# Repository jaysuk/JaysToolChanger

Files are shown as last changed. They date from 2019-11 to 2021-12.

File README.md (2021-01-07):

# JaysToolChanger
Tool Changing 3D printer with a larger print volume and minimal machined parts.

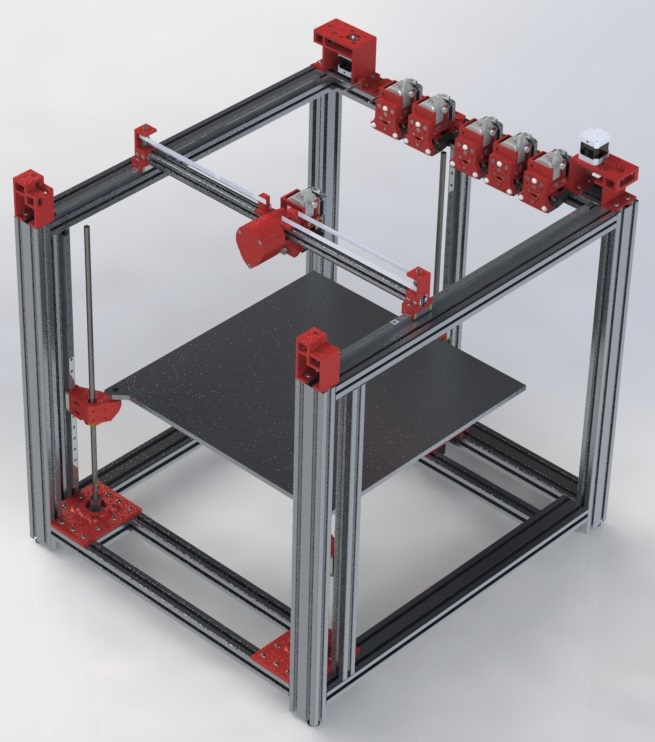
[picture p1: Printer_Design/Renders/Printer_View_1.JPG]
Printer


The design is pretty much completed and I am currently ordering and printing components.
I plan to have it built within the next couple of months or so.

# Design Goals
* Use the duet 3 board plus appropriate expansion boards
* Have direct drive tools
* Use a motor on the carriage for the tool changer (although this may be upgraded down the line to cable driven)
* Have 3 point levelling
* Have a minimal number of machined components (at the moment this stands at the bed and the locking pin).
* Design everything in Solidworks
* Stay E3D Tool compatible (my tools use 10mm balls but this wouldn't affect the tool changer)

# The todo list
These aren't in any particular order
* Design an exnclosure
* Add a method of wiping each tool
* Swap to the E3D Hermes when available
* Release duet config files
* Sort out electronics layout
* Update the bed model to include embedded magnets for swappable print surfaces
* Determine location of end stops for X, Y and Z
	
# Supplied Formats
The design will be supplied in the following file formats
* Solidworks - All files in native 2019 format. This is what I use to model everything
* Step - All files will be available as step. The assembly step files are segregated.
* STL - All printables
* 3MF - All printables
* PDF - Drawings for all machined parts

I welcome any feedback on this printer and will be working more on the design over the coming weeks.

# About Me
I'm a mechaical engineer by trade and have been dabbling in 3D printing for the last 9 years.
I have owned a number of printers, mainly cartesian or delta types. This is my first coreXY.
I plan on posting on [My Blog](https://www.jayuk.org/) with my build progression.
There is a [Discord Server](https://discord.gg/txqEmK). Come and join me for a chat!

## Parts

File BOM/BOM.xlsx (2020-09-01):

ITEM NO. | PART NUMBER | DESCRIPTION | QTY. | Purchased or Printed | Link
1 | 30x60 - 700 Front Upright | Series 6 30x60 extrusion 700mm long | 2 | Purchased
2 | 30x60 - 700 Bottom Side | Series 6 30x60 extrusion 700mm long | 2 | Purchased
3 | 30x60 - 700 Top Side | Series 6 30x60 extrusion 700mm long | 2 | Purchased
4 | 30x60 - 700 Back Upright | Series 6 30x60 extrusion 700mm long | 2 | Purchased
5 | 30x30 - 610 Z Upright | Series 6 30x30 extrusion 610mm long | 3 | Purchased
6 | 30x60 - 660 Centre | Series 6 30x60 extrusion 660mm long | 2 | Purchased
7 | 30x30 - 600 Centre Front Bottom | Series 6 30x30 extrusion 600mm long | 2 | Purchased
8 | Z Motor Mount Left |  | 1 | Printed
9 | M5x6x7 - Heat Set Insert |  | 20 | Purchased
14 | BS EN ISO 4762 M5 x 20 - 20N |  | 12 | Purchased
15 | Coupling 6.35x10 |  | 3 | Purchased
16 | 2020 Nut - M6 |  | 27 | Purchased
17 | BS EN ISO 7380 - M6 x 10 - 10N |  | 27 | Purchased
18 | Z Motor Mount Right |  | 1 | Printed
19 | Bed |  | 1 | Machined
23 | Button M3x8 |  | 20 | Purchased
24 | Rail 550mm | MGN12H Linear Rail 550mm Long with Block | 3 | Purchased
25 | 2020 Nut - M3 |  | 118 | Purchased
26 | BS EN ISO 4762 M3 x 10 - 10N |  | 118 | Purchased
27 | Z Block Left |  | 1 | Printed
28 | M3x10x5 - Heat Set Insert |  | 3 | Purchased
29 | M3x6x5 - Heat Set Insert |  | 32 | Purchased
30 | TR10 Nut |  | 3 | Purchased
31 | Ball Stud - Haydn |  | 3 | Purchased
32 | BS EN ISO 7380 - M3 x 6 - 6N |  | 14 | Purchased
33 | 30x30 - 540 Centre | Series 6 30x30 extrusion 600mm long | 1 | Purchased
34 | TR10 Thread | TR10 Threaded Rod 600mm Long | 3 | Purchased
35 | Z Motor Mount Back |  | 1 | Printed
36 | Z Block Right |  | 1 | Printed
37 | Z Block Back |  | 1 | Printed
38 | Rail 650mm | MGN12H Linear Rail 650mm Long with Block | 2 | Purchased
39 | 20x20 - 660 X Carriage | Series 5 20x20 extrusion 660mm long | 1 | Purchased
40 | Y Carriage Base |  | 2 | Printed
41 | M4x6x6 - Heat Set Insert |  | 8 | Purchased
42 | BS EN ISO 10642 - M3 x 10 - 10N |  | 4 | Purchased
43 | Y Carriage Top |  | 2 | Printed
44 | 5x7x0.3 shim |  | 22 | Purchased | https://www.aliexpress.com/item/32924107429.html?spm=a2g0s.9042311.0.0.5b684c4dTJyEaW
45 | Toothed Idler | 20t toothed idler with teeth for 10mm 2GT belt | 8 | Purchased | https://www.aliexpress.com/item/33023133633.html?spm=a2g0s.9042311.0.0.3df64c4d0Ccrgg
 | Toothed Idler | 20t toothed idler without teeth for 10mm 2GT belt | 4 | Purchased | https://www.aliexpress.com/item/33023133633.html?spm=a2g0s.9042311.0.0.3df64c4d0Ccrgg
 | 2GT Belt |  | 8m | Purchased | https://www.aliexpress.com/item/32952396111.html?spm=a2g0s.9042311.0.0.3df64c4d0Ccrgg
49 | Right Motor Mount |  | 1 | Printed
54 | Pulley | 20t Timing Belt pulley for 10mm belt | 2 | Purchased | https://www.aliexpress.com/item/33023279793.html?spm=a2g0s.9042311.0.0.3df64c4d0Ccrgg
55 | M5x10x7 - Heat Set Insert |  | 2 | Purchased
56 | BS EN ISO 7380 - M5 x 25 - 25N |  | 8 | Purchased
57 | BS 4168-3 - M5 x 10-N |  | 2 | Purchased
58 | 2020 Nut - M5 |  | 8 | Purchased
59 | BS EN ISO 7380 - M5 x 12 - 12N |  | 8 | Purchased
60 | Front Right Idler Mount |  | 1 | Printed
61 | Left Motor Mount |  | 1 | Printed
62 | Front Left Idler Mount |  | 1 | Printed
64 | MGN9-H | MGN9H Linear Rail 600mm Long | 1 | Purchased
65 | X Carriage Base |  | 1 | Printed
66 | M3x4x5 - Heat Set Insert |  | 28 | Purchased
67 | M4x10x6 - Heat Set Insert |  | 5 | Purchased
68 | 30x30 - 85 Z Motor Support | Series 6 30x30 extrusion 85mm long | 2 | Purchased
69 | 14HR08-0654S - Nema 14 Motor |  | 1 | Purchased
70 | 14t gear mod1 |  | 1 | Purchased | https://www.ebay.co.uk/itm/14T-Mod1-M1-Steel-Pinion-Gear-5mm-bore-14-tooth-hardened-rc-crawler-car/182340380462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
71 | 30t gear MOD1 |  | 1 | Purchased | https://www.ebay.co.uk/itm/30T-M1-MOD1-Steel-Pinion-Gear-hardened-5mm-bore-30-tooth-rc-car/122207015211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
72 | Locking Pin |  | 1 | Machined
73 | 91585A371 | M3 12mm dowel pin | 1 | Purchased
74 | BS 4168-2 - M3 x 2-N |  | 1 | Purchased
75 | W 605-2Z_PART1 | 6052Z bearing | 2 | Purchased | https://www.ebay.co.uk/itm/605ZZ-605-2Z-Metal-Shielded-Deep-Groove-Ball-Bearing-5x14x5mm/123276545874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
79 | Tool Changer Box Back |  | 1 | Printed
80 | Tool Changer Box Cover |  | 1 | Printed
81 | Z Switch | DB1C-A1AA | 2 | Purchased | https://smile.amazon.co.uk/dp/B00FV1TBBM/ref=pe_3187911_189395841_TE_3p_dp_1
82 | BS EN ISO 7045 - M3 x 4 - Z - 4N |  | 1 | Purchased
83 | M2x6x3.5 - Heat Set Insert |  | 2 | Purchased
84 | BS EN ISO 7380 - M4 x 12 - 12N |  | 4 | Purchased
85 | BS EN ISO 7045 - M2 x 10 - Z - 10N |  | 4 | Purchased
87 | Coupling Plate | Coupling Plate | 1 | Printed
88 | 91585A457 | M4 Dowel Pin, 20mm long | 6 | Purchased
89 | M2x8x3.5 - heat Set Insert |  | 2 | Purchased
90 | BS EN ISO 10642 - M4 x 16 - 16N |  | 3 | Purchased
91 | Main Plate |  | 6 | Printed
92 | Locking Plate |  | 6 | Printed
93 | BS EN ISO 10642 - M3 x 8 - 8N |  | 22 | Purchased
94 | m4_10mm_threaded_ ball |  | 18 | Purchased | https://www.aliexpress.com/item/32761330456.html?spm=a2g0s.9042311.0.0.5b684c4dTJyEaW
95 | BS EN ISO 10642 - M4 x 8 - 8N |  | 36 | Purchased
96 | BMG Mount |  | 6 | Printed
97 | bondtech_bmg_simplif ied |  | 6 | Purchased | https://www.aliexpress.com/item/4000072198732.html?spm=a2g0s.9042311.0.0.3df64c4d0Ccrgg
98 | E3D Hotend V6 |  | 6 | Purchased | https://e3d-online.com/v6-all-metal-hotend
105 | 17HS10-0704S - Nema 17 Motor |  | 6 | Purchased | https://e3d-online.com/slimline-motor
106 | M4x4x6 - Heat Set Insert |  | 60 | Purchased
107 | Arm Holder |  | 12 | Printed
108 | BS EN ISO 4762 M4 x 6 - 6N |  | 24 | Purchased
109 | 4010 Blower |  | 12 | Purchased
110 | Fan Mount 1 |  | 6 | Printed
111 | M2x4x3.5 - Heat Set Insert |  | 24 | Purchased
112 | Fan Mount 2 |  | 6 | Printed
113 | BS EN ISO 7045 - M2 x 5 - Z - 5N |  | 30 | Purchased
114 | Tool Holder Base |  | 6 | Printed
115 | BS EN ISO 8734 - 5 x 50 - A - St |  | 12 | Purchased | https://www.ebay.co.uk/itm/50x-Parallel-pin-dowel-pin-DIN-7-Stainless-steel-A1-A2-5X50MM/392257309488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
116 | 2020 Nut - M4 |  | 18 | Purchased
117 | BS EN ISO 7380 - M4 x 10 - 10N |  | 26 | Purchased
118 | BS 4168-4 - M4 x 5-N |  | 18 | Purchased
119 | BS EN ISO 4762 M3 x 16 - 16N |  | 12 | Purchased
120 | BS EN ISO 7380 - M6 x 12 - 12N |  | 8 | Purchased
121 | BS EN ISO 7380 - M4 x 8 - 8N |  | 4 | Purchased
122 | 2020 Nut Series 5 - M5 |  | 2 | Purchased
123 | BS EN ISO 4762 M5 x 45 - 22N |  | 2 | Purchased
124 | 2020 Nut Series 5 - M4 |  | 8 | Purchased
125 | 2020 Nut Series 5 - M3 |  | 30 | Purchased
126 | BS EN ISO 4762 M3 x 8 - 8N |  | 30 | Purchased
127 | Foot | M6 mounting foot | 4 | Purchased | https://www.ebay.co.uk/itm/Adjustable-tilt-Levelling-feet-foot-M6x25mm-kitchen-desk-table-sink-prep-bench/283463635084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
 | 24v Power Supply |  | 1 | Purchased | https://www.aliexpress.com/item/32981871190.html?spm=a2g0s.9042311.0.0.5b684c4dTJyEaW
 | Nema 23 |  | 3 | Purchased | https://www.omc-stepperonline.com/nema-23-stepper-motor/nema-23-bipolar-0-9deg-1-26nm-178-4oz-in-2-8a-2-5v-57x57x56mm-4-wires.html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
 | Nema 17 Motor |  | 2 | Purchased | https://www.omc-stepperonline.com/nema-17-bipolar-0-9deg-46ncm-65-1oz-in-2a-2-8v-42x42x48mm-4-wires-full-d-cut-shaft.html

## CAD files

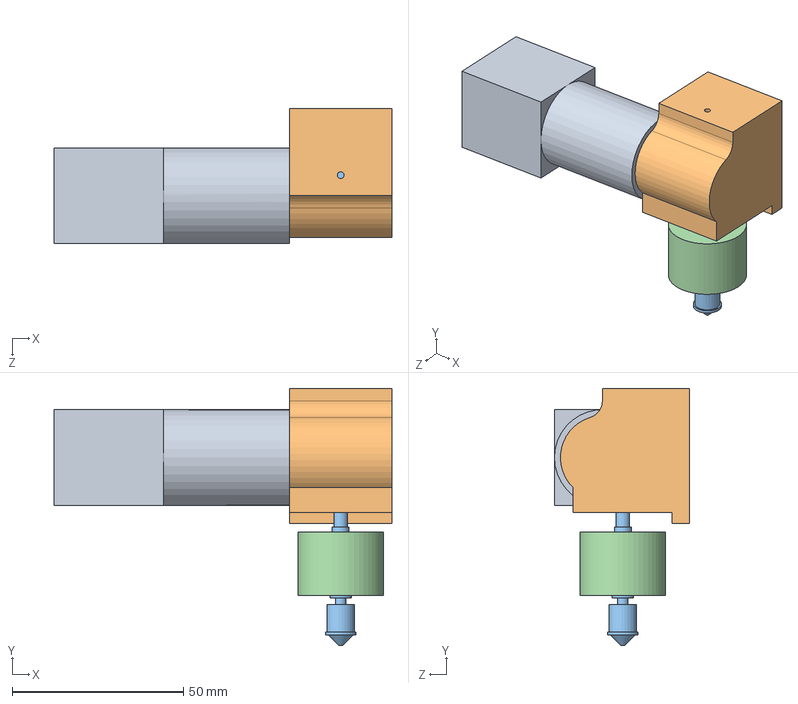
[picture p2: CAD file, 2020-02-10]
Printer_Design/Drawings/Get3D Extruder.SLDASM
98.8 x 75.2 x 39.5 mm
Motor
Extruder part 1
nozzle
Heat Sink

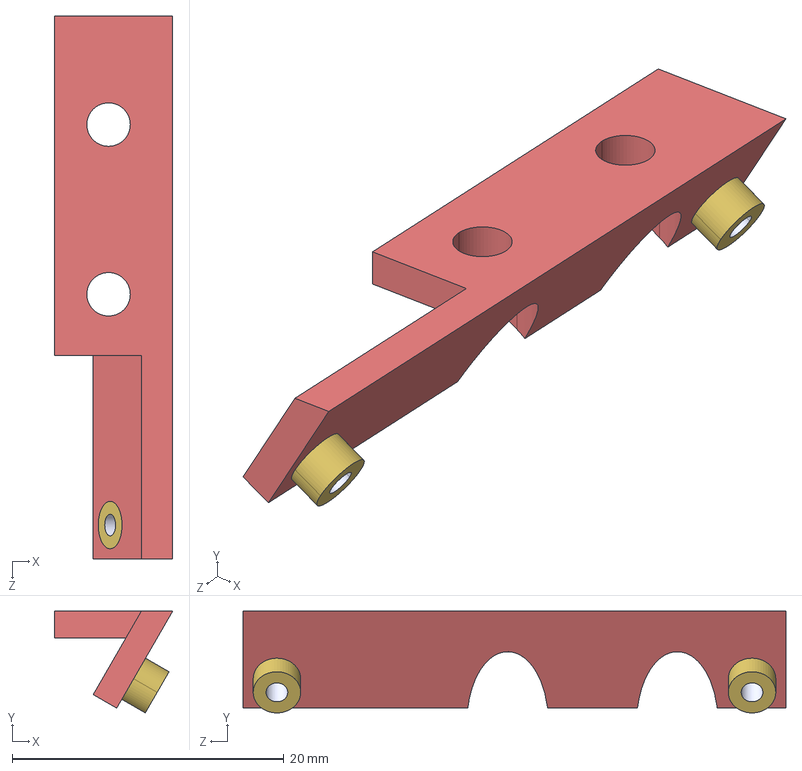
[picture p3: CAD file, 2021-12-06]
Printer_Design/STEP/Assemblies/Fan Mount 1 Assembled.step
8.73 x 7.50 x 40.0 mm
Fan Mount 1
M2x4x3.5 - Heat Set Insert x 2

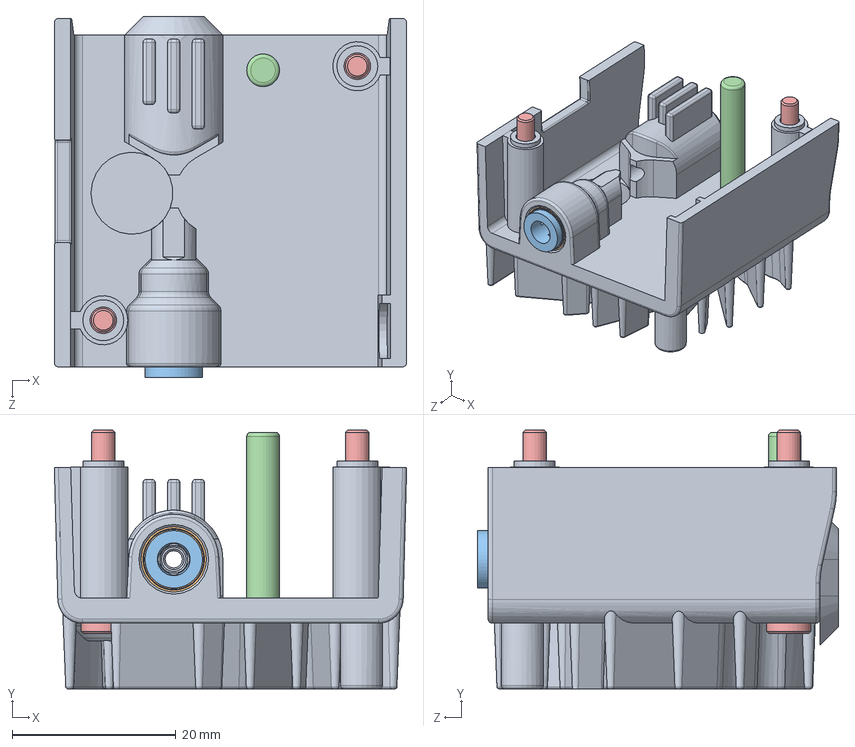
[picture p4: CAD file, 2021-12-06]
Printer_Design/Solidworks/Heatsink Assembly.sldasm
43.0 x 31.6 x 44.0 mm
Heatsink
PFTE Coupler Insert
PTFE Coupler Retainer
Lever Axis
M3x22 Hex Screw x 2

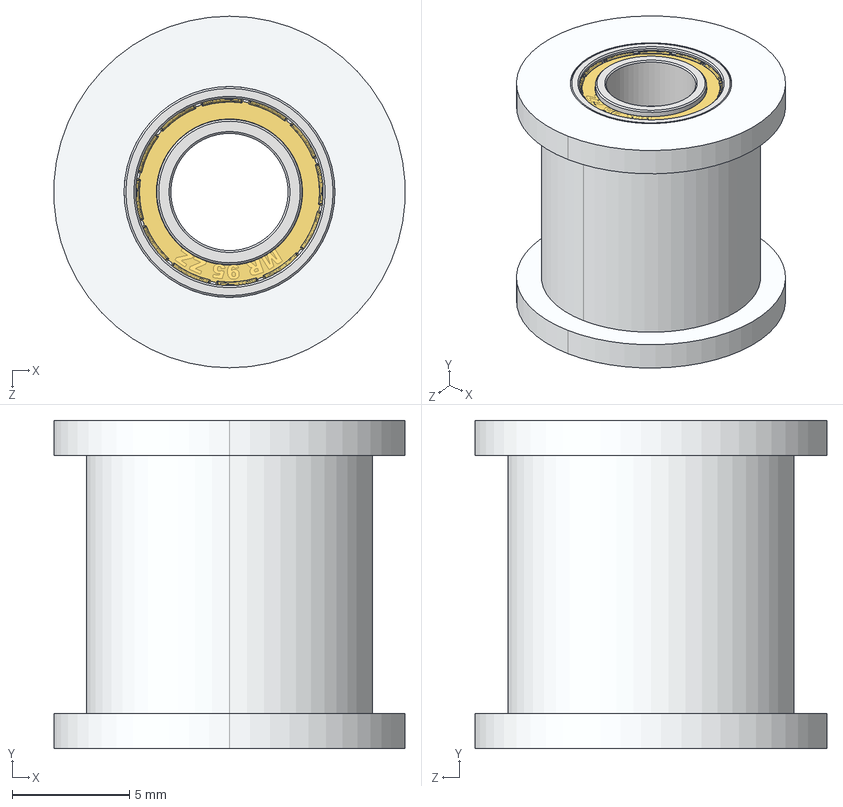
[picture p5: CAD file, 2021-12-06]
Printer_Design/STEP/Assemblies/Toothed Idler Assembled.step
15.0 x 14.0 x 15.0 mm
Toothed Idler
mr95zz-cen x 4
mr95zz-ext x 2
mr95zz-int x 2

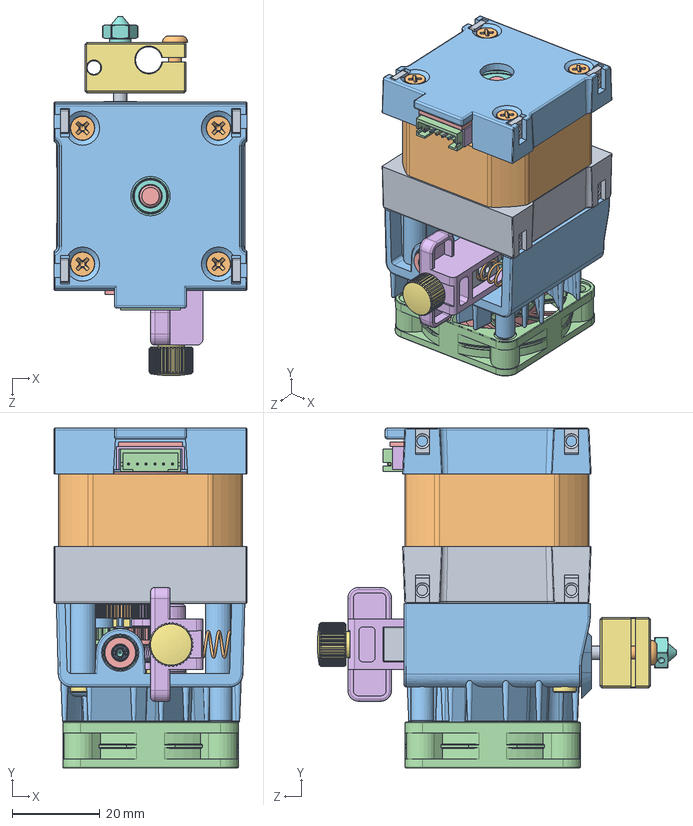
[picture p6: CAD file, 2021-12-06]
Printer_Design/Solidworks/E3D Hemera - Purchased.SLDASM
44.0 x 77.6 x 82.0 mm
Frontplate
Stator
Baseplate
ConnectrorBody (2)
PCB (3)
Insulation (2)
Axis&Rotor
Drive Gear S
Ballbearing
BallBearing2
M3 Square Nut x 9
M3x_-Screw x 4
Heatsink
PFTE Coupler Insert
PTFE Coupler Retainer
Lever Axis
M3x22 Hex Screw x 2
3.5x23.5mm Shaft (1)
10mm Bearing x 2
Drive Gear L
2.3mm Gear Spacer
Dual Transmission Gear
Filament Drive Gear Fixed
Lever Arm
Tensioner Spanner
Tensioner Push-Block
Tensioner Spring-Block
Spring
Gear Axis
4x6x8 Igus Bushing
Dual Transmission Gear (1)
Filament Drive Gear
Heater Block
Nozzle
Heat Break
M3 Button Head Screw
M3 Grub Screw
Fan Housing
Fan Propeller
M3x13 Self-Cutting Screw x 2

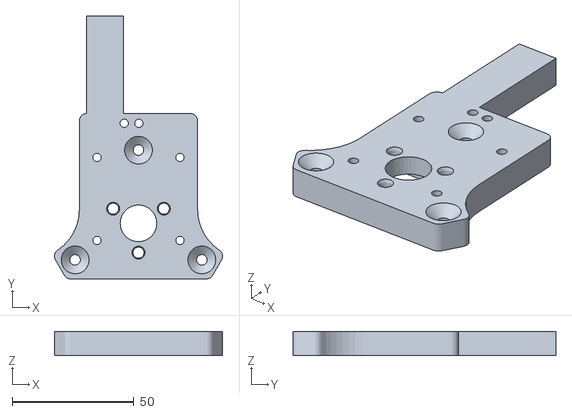
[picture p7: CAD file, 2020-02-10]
Printer_Design/STL/Main Plate - Hemera.STL
68.9 x 107.8 x 10.00

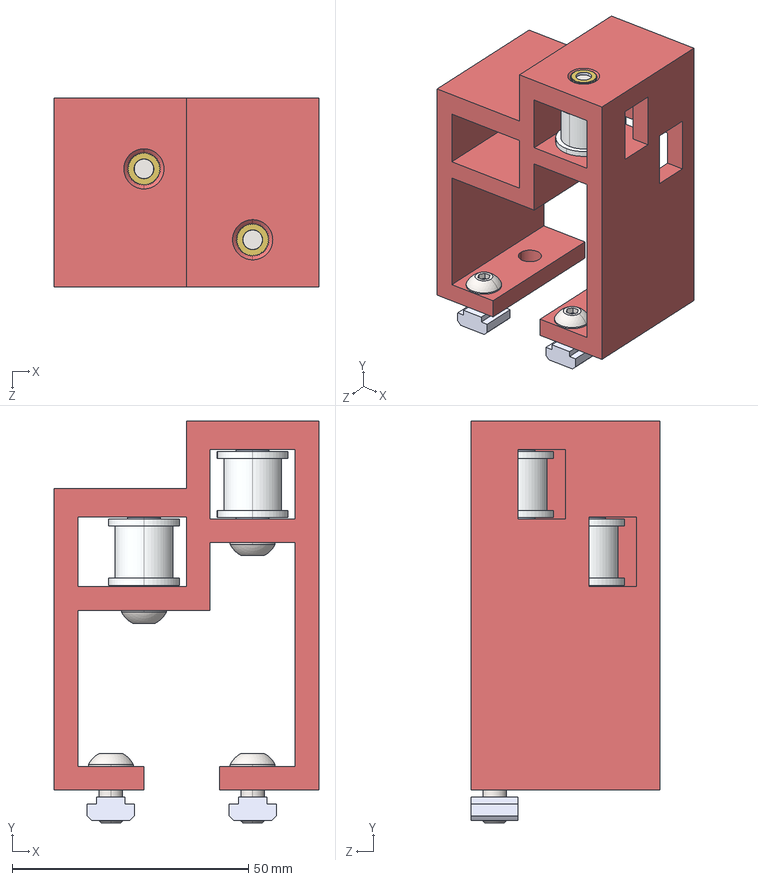
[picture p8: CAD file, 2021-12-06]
Printer_Design/STEP/Assemblies/Front Right Idler Mount Assembled.step
56.0 x 85.1 x 40.0 mm
Front Right Idler Mount
Toothed Idler x 2
mr95zz-cen x 8
mr95zz-ext x 4
mr95zz-int x 4
5x7x0.3 shim x 4
M5x6x7 - Heat Set Insert x 2
socket button head screw_bsi_BS EN ISO 7380 - M5 x 25 - 25N x 2
2020 Nut - M5 x 2
socket button head screw_bsi_BS EN ISO 7380 - M5 x 12 - 12N x 2

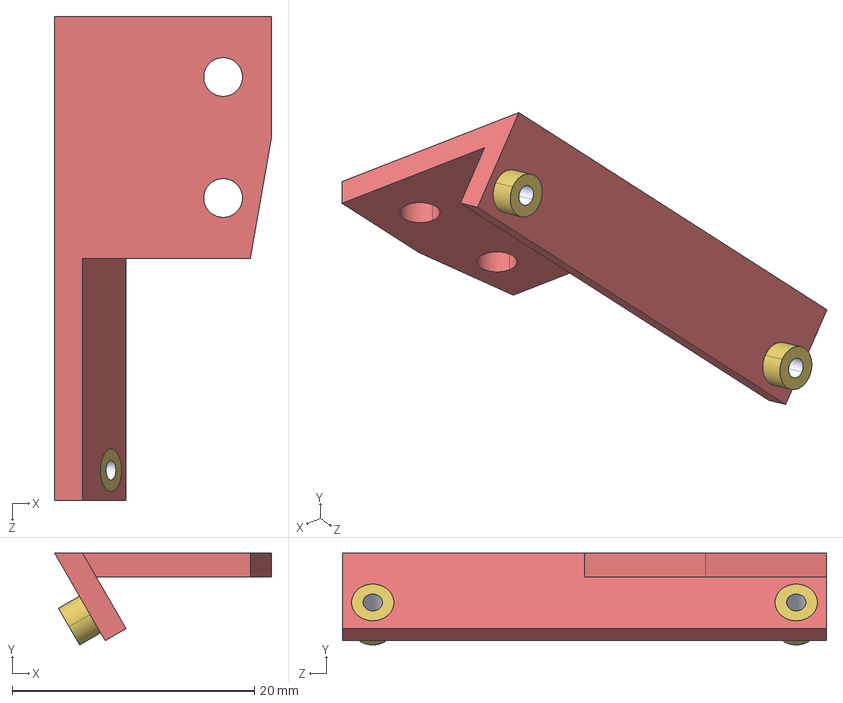
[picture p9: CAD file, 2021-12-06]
Printer_Design/STEP/Assemblies/Fan Mount 2 Assembled.step
17.9 x 7.60 x 40.0 mm
Fan Mount 2
M2x4x3.5 - Heat Set Insert x 2

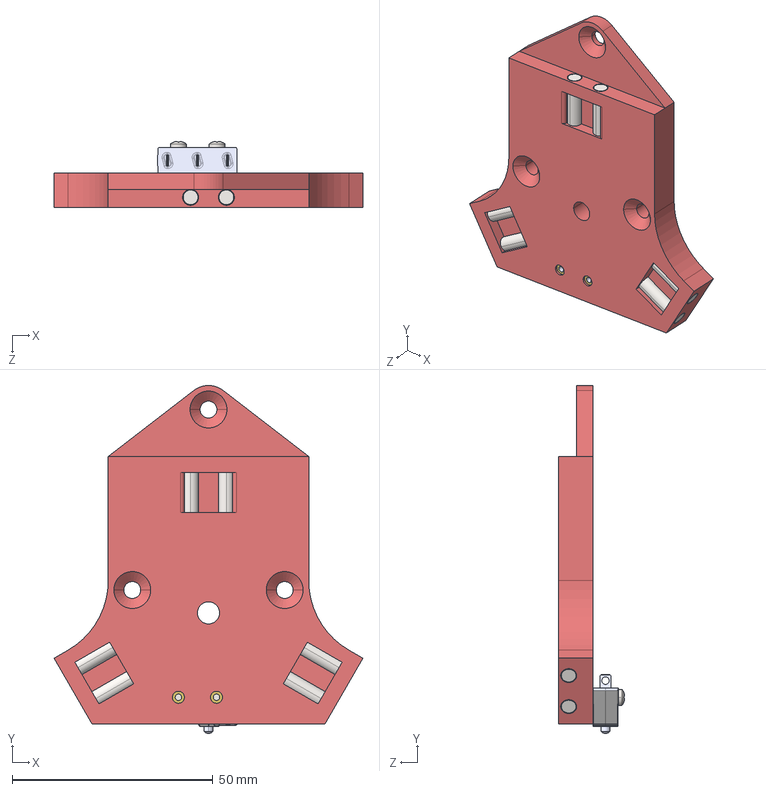
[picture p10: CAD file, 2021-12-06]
Printer_Design/STEP/Assemblies/Coupling Plate Assembled.step
77.0 x 86.8 x 16.6 mm
Coupling Plate_Carriage Coupler Plate
dowel_pin_4mm_d_20mm_l_91585A457_91585A457 x 6
M2x8x3.5 - heat Set Insert x 2
Z Switch
pan head cross recess screw_bsi_BS EN ISO 7045 - M2 x 10 - Z - 10N x 2

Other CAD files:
Printer_Design/Solidworks/D_SMA.SLDASM
Printer_Design/Solidworks/Duet/6HC/dr331.sldasm
Printer_Design/Solidworks/Duet/6HC/R_0402_1005Metric.sldasm
Printer_Design/Solidworks/Duet/6HC/TO-252-2.sldasm
Printer_Design/Solidworks/JST_ZH_S3B-ZH_1x03P1.50mm_Horizontal.SLDASM
Printer_Design/Solidworks/Duet/6HC/B6B-ZR.sldasm
Printer_Design/Solidworks/DFN-8-1EP_3x3mm_P0.5mm_EP1.66x2.38mm.SLDASM
Printer_Design/Solidworks/Duet/6HC/CP_Elec_6.3x7.7.sldasm
Printer_Design/Solidworks/Duet/6HC/Molex_KK-254_AE-6410-03A_1x03_P2.54mm_Vertical.sldasm
Printer_Design/3MF/Arm Holder.3mf
Printer_Design/3MF/BMG Mount.3mf
Printer_Design/3MF/Coupling Plate.3mf
Printer_Design/3MF/Fan Mount 1.3mf
Printer_Design/3MF/Fan Mount 2.3mf
Printer_Design/3MF/Front Left Idler Mount.3mf
Printer_Design/3MF/Front Right Idler Mount.3mf
Printer_Design/3MF/Left Motor Mount.3mf
Printer_Design/3MF/Locking Plate.3mf
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

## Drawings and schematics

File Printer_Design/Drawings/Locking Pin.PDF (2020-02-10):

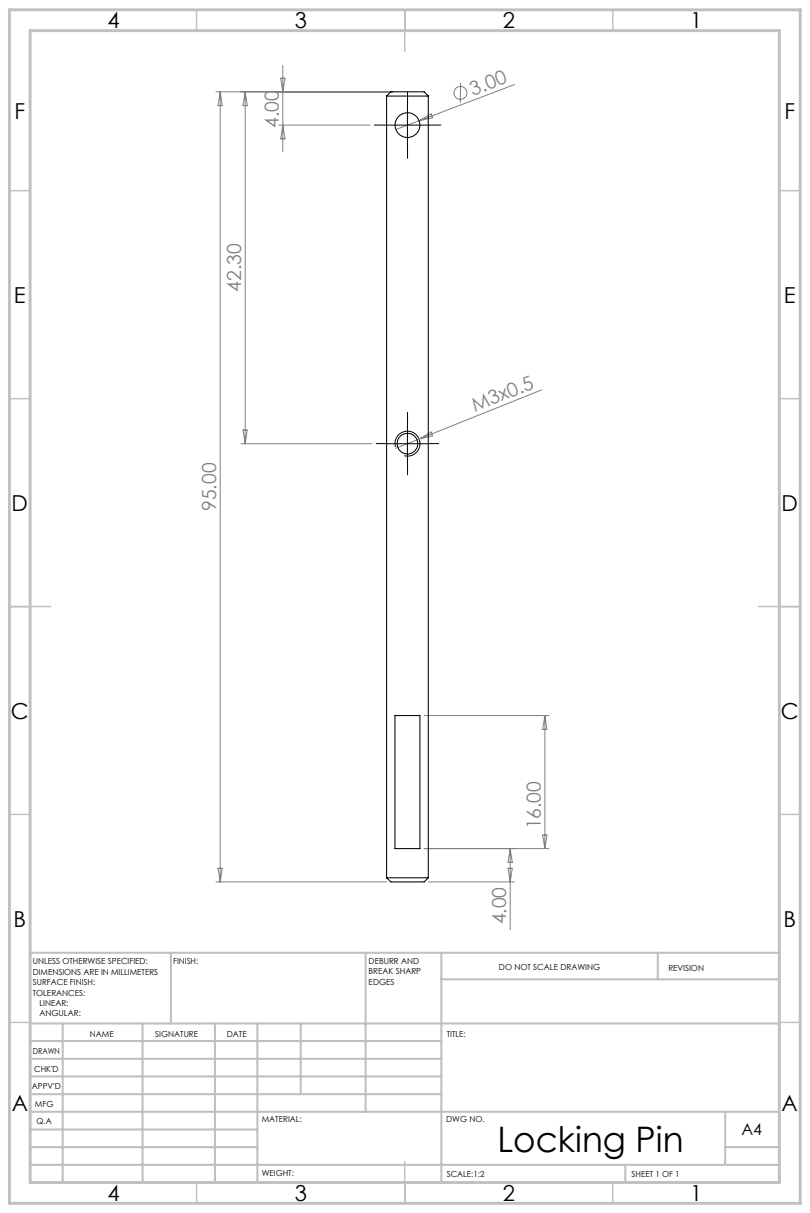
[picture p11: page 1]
FINISH:; DEBURR AND; BREAK SHARP; DO NOT SCALE DRAWING; REVISION; SCALE:1:2; SHEET 1 OF 1

UNLESS OTHERWISE SPECIFIED:
DIMENSIONS ARE IN MILLIMETERS
SURFACE FINISH:
TOLERANCES:
LINEAR:
ANGULAR:

NAME | SIGNATURE | DATE | | | | TITLE:

DRAWN
CHK'D
APPV'D
MFG
Q.A | | | | MATERIAL: | DWG NO. Locking Pin | A4

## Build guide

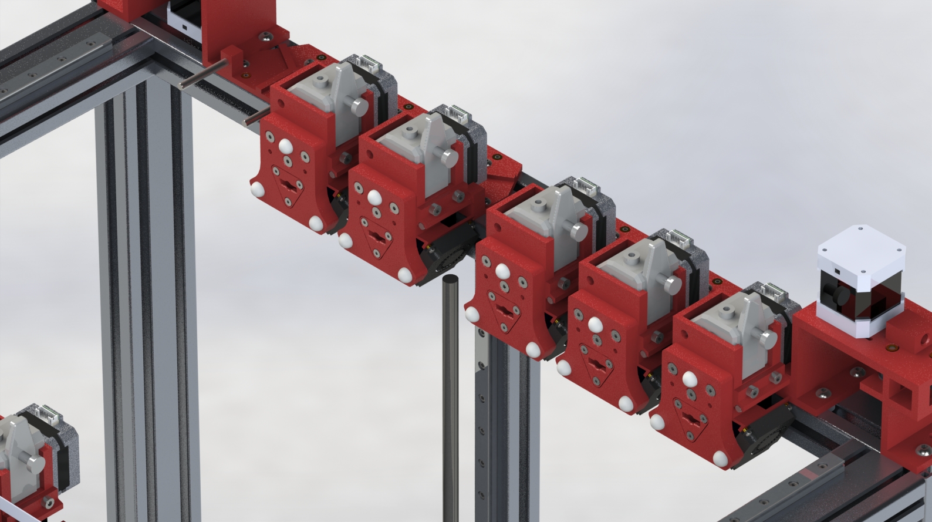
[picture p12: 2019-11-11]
Printer_Design/Renders/Printer_View_3.JPG

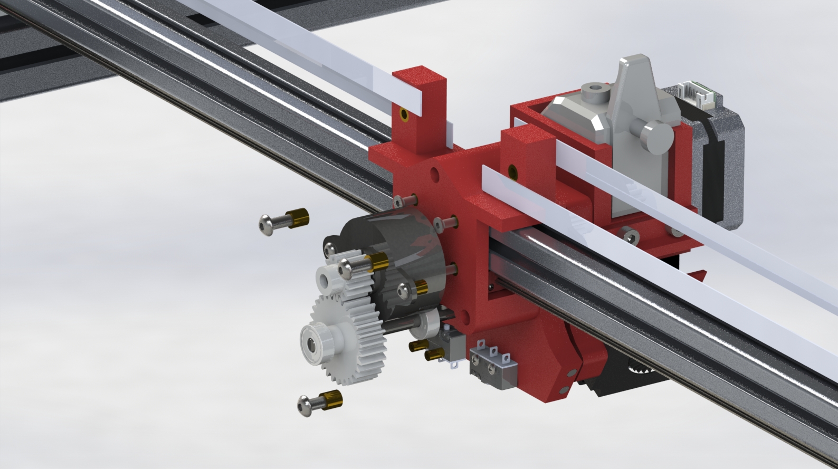
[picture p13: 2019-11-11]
Printer_Design/Renders/Printer_View_4.JPG

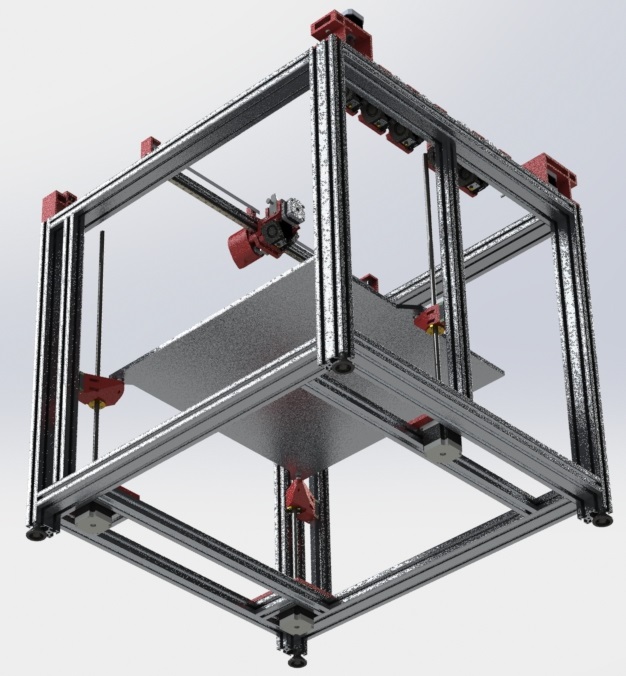
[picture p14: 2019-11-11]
Printer_Design/Renders/Printer_View_2.JPG

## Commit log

2019-11-11 Initial Design Commit
    Initial Design Commit
    [-MR95ZZ-assem.SLDASM, -MR95ZZ-assem.step, 14HR08-0654S - Nema 14 Motor.SLDPRT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]
2019-11-11 Update to naming
    [-MR95ZZ-assem.SLDASM, -MR95ZZ-assem.step, 14HR08-0654S - Nema 14 Motor.SLDPRT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]
2019-11-12 Modified toolchanger
    Removed the bottom fixing screw for the cover and replaced it with 2 on the sides to increase clearance for the z probe if the bed is really tilted.
    Increased the inner diameter by 1mm as the 30t gear is a snug fit.
    Added some flats where the motor sits to make sure it fits.
    [5x14x5 Bearing.sldasm, BMG Direct Drive Tool Assembled.SLDASM, Coupling Plate Assembled.SLDASM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]
2019-11-15 First release of the BOM
    [BOM.xlsx]
2020-02-10 Updating to current design.
    Please note, all the STLs and 3MFs require reproducing
    [-MR95ZZ-assem.SLDASM, 10mm Bearing.sldprt, 17HS10-0704S - Nema 17 Motor - Purchased.SLDPRT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]
2020-09-04 more tweaks
    [Clamp - Printed.SLDPRT, Clamp - Printed.STL, Coupling Plate - Printed.SLDPRT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]
